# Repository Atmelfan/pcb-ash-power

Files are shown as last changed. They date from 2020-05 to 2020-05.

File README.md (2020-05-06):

# ASH Power distribution board

This board manages power control and distribution for my Octapod.

The power board has the following responsibilites:
* Regulate servo voltage from 2 or 3S Li-ion battery packs.
* Measure voltage and current to servos.
* Supply the main board with power (not regulated).
* Provide soft-start functionality for servos.
* Control power on/off to servos.
* Protect batteries with UVLO and OVLO.
~~* Integrated charger using external USB-C supply.~~
* Provide an interface for both main board MCU(I2C) and NVM(serial-SCPI).

[Schematic](https://github.com/Atmelfan/pcb-ash-power/raw/master/schematics.PDF)

[Assembly diagram](https://github.com/Atmelfan/pcb-ash-power/raw/master/assembly.PDF)

[Bill of material](https://htmlpreview.github.io/?https://github.com/Atmelfan/pcb-ash-power/blob/master/bom.html)

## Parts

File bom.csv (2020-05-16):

value | Line # | Name | Description | Designator | Quantity | Footprint | Manufacturer 1 | Manufacturer Part Number 1 | Manufacturer Lifecycle 1 | Supplier 1 | Supplier Part Number 1 | Supplier Unit Price 1 | Supplier Subtotal 1
 |  | INA3221 | Triple-Channel, High-Side Measurement. Shunt and Bus Voltage Monitor with I 2 C- and SMBUS-Compatible Interface | U1102, U1302, U1502, U1702, U2202, U2402, U2602, U2802 | 8 | QFN65P400X400X100_HS-17N_INA3221 | Texas Instruments | INA3221AIRGVR | Volume Production | Digi-Key | 296-INA3221AIRGVRDKR-ND | 39.18 | 313.42
 |  | ltc4421xuhe | High Power Prioritized PowerPath Controller | U3, U1004, U2004 | 3 | QFN50P500X600X80_HS-37N_LTC4421 | Analog Devices | LTC4421CUHE#PBF | Volume Production | Digi-Key | 161-LTC4421CUHE#PBF-ND | 96.86 | 290.59
 |  | EPC2030 | GaN Enhancement Mode Power Transistor | Q1006, Q1007, Q2006, Q2007 | 4 | epc2030_die | EPC | EPC2030ENGRT | Volume Production | Digi-Key | 917-EPC2030ENGRDKR-ND | 64.48 | 257.9
22u |  | cap | Capacitor | C1028-1031, C1037-1040, C2028-2031, C2037-2040 | 16 | CAPC3225X14N | Murata | GRM32ER71E226KE15L | Volume Production | Digi-Key | 490-5313-6-ND | 15.22 | 243.49
 |  | TPS1HB08A-Q1 | 40-V, 8-mO Single-Channel Smart High-Side Switch | U1100, U1300, U1500, U1700, U2200, U2400, U2600, U2800 | 8 | TSOP65P640X120_HS-17N_TPS1HB08 | Texas Instruments | TPS1HB08AQPWPRQ1 | Unknown | Digi-Key | 296-TPS1HB08AQPWPRQ1DKR-ND | 25.4 | 203.17
 |  | ltc7800 | Low IQ, 60V, High Frequency Synchronous Step-Down Controller | U1002, U2002 | 2 | QFN50P300X400X80_HS-21N_LTC7800 | Analog Devices / Linear Technology | LTC7800EUDC#PBF | Volume Production | Digi-Key | LTC7800EUDC#PBF-ND | 85.25 | 170.49
0R01 |  | res_4t | Resistor | R47, R1018, R1108, R1109, R1111, R1308, R1309, R1311, R1508, R1509, R1511, R1708, R1709, R1711, R2018, R2208, R2209, R2211, R2408, R2409, R2411, R2608, R2609, R2611, R2808, R2809, R2811 | 27 | 4T_RESC1632X05N | Cyntec | RL1632T4F-R010-FNH | Unknown | Digi-Key | 2037-RL1632T4F-R010-FNHDKR-ND | 6.03 | 162.76
 |  | SiR158DP | N-Channel 30 V (D-S) MOSFET | Q1008, Q1009, Q1011, Q1012, Q2008, Q2009, Q2011, Q2012 | 8 | SON127P620X112_HS-9N_POWERPAK_SO8 | Vishay Siliconix | SIR158DP-T1-GE3 | Volume Production | Digi-Key | SIR158DP-T1-GE3CT-ND | 17.72 | 141.75
 |  | LTC4370xMS | Two-Supply Diode-OR Current Balancing Controller | U4 | 1 | TSSOP50P510X110-16N_ltc4421 | Analog Devices / Linear Technology | LTC4370IMS#PBF | Volume Production | Digi-Key | LTC4370IMS#PBF-ND | 135.84 | 135.84
 |  | IRFH3702 | HEXFET Power MOSFET | Q9, Q10 | 2 | PQFN67P300X300X100-8N | International Rectifier | IRFH3702TRPBF | Volume Production | Digi-Key | IRFH3702TRPBFCT-ND | 55.23 | 110.46
 |  | pca9633dp2 | 4-bit Fm+ I2C-bus LED driver | U1101, U1301, U1501, U1701, U2201, U2401, U2601, U2801 | 8 | TSSOP50P490X110-10N_PCA9633DP2 | NXP Semiconductors | PCA9633DP2,118 | Volume Production | Digi-Key | 568-3237-6-ND | 13.09 | 104.74
 |  | 74LV4T125A | Quadruple Bus Buffer Gates With 3-State Outputs | U1103, U1303, U1503, U1703, U2203, U2403, U2603, U2803 | 8 | QFN50P350X350X100_HS-15N | Texas Instruments | SN74LV4T125RGYR | Volume Production | Digi-Key | 296-40546-1-ND | 9.45 | 75.6
 |  | ina219aidcnx | INA219 Zero-Drift, Bidirectional Current/Power Monitor With I2C Interface | U10, U1000, U2000 | 3 | TSOP65P280X145-8N | Texas Instruments | INA219AIDCNR | Volume Production | Digi-Key | 296-23770-1-ND | 23.23 | 69.69
1u |  | SER2009-102ML | Shielded Power Inductor | L1001, L2001 | 2 | SER20xx | Coilcraft | SER2009-102MLB | Volume Production | Mouser | 994-SER2009-102MLB | 25.1 | 50.2
 |  | STM32F103C8T6 | ARM Cortex-M3 32-bit MCU, 64 KB Flash, 20 KB Internal RAM, 37 I/Os, 48-pin LQFP, -40 to 85 degC, Tray | U2 | 1 | STM-LQFP48_N | STMicroelectronics | STM32F103C8T6 | Volume Production | Digi-Key | 497-6063-ND | 48.63 | 48.63
 |  | 430450617 | Micro-Fit 3.0 Vertical Header, 3.00mm Pitch, Dual Row, 6 Circuits, with PCB Press-fit Metal Retention Clip, Gold, Glow-Wire Capable, Black | J3 | 1 | 430450617 | Molex | 43045-0617 | Volume Production | Digi-Key | WM23255CT-ND | 39.08 | 39.08
 |  | DFLS2100 | 2.0A HIGH VOLTAGE SCHOTTKY BARRIER RECTIFIER | D11, D12, D17, D1000, D2000 | 5 | SODFL370X100-2N_DFLS2100 | Diodes Zetex | DFLS2100-7 | Volume Production | Digi-Key | DFLS2100-7DIDKR-ND | 5.61 | 28.05
 |  | 1054550101 | USB TYPE C REC MIDDLE MOUNT TYPE | J8 | 1 | 1054550101 | Molex | 105455-0101 | Unknown | Digi-Key | WM17904DKR-ND | 23.72 | 23.72
 |  | pca9685bs | 16-channel, 12-bit PWM Fm+ I2C-bus LED controller | U8 | 1 | QFN65P600X600X100_HS-29N_PCA9685BS | NXP USA | PCA9685BS,118 | Unknown | Digi-Key | 568-5305-6-ND | 23.43 | 23.43
 |  | IRFH3702 | HEXFET Power MOSFET | Q5-8 | 4 | PQFN67P300X300X100-8N | International Rectifier | IRFH3702TRPBF | Volume Production | Digi-Key | IRFH3702TRPBFCT-ND | 5.61 | 22.44
 |  | bq2961xx | BQ296xxx Overvoltage Protection for 2-Series, 3-Series, and 4-Series Cell Li-Ion Batteries with Regulated Output Supply | U1003, U2003 | 2 | SON50P200X80_HS-9N-BQ2960XX | Texas Instruments | BQ296106DSGT | Volume Production | Digi-Key | 296-BQ296106DSGTDKR-ND | 9.84 | 19.69
22u |  | cap | Capacitor | C2, C3, C34, C35 | 4 | CAPC3216X14N | Samsung | CL31A226KAHNNNE | Volume Production | Digi-Key | 1276-3047-6-ND | 4.82 | 19.29
1m5 |  | res_4t | Resistor | R16, R1028, R2028 | 3 | 4T_RESC1632X05N | Cyntec | RL1632T4F-R001-FNH | Unknown | Digi-Key | 2037-RL1632T4F-R001-FNHDKR-ND | 5.91 | 17.72
3m3 |  | SRR4028 |  | L1, L2 | 2 | SRR4028 | Bourns | SRR4028-3R3Y | Volume Production | Digi-Key | SRR4028-3R3YCT-ND | 8.56 | 17.13
 |  | BAS40-5 | Diode Common Cathode | D2, D3, D7, D8, D13, D1003, D2003 | 7 | SOT23_CC | Diodes | BAS40-05-7-F | Volume Production | Digi-Key | BAS40-05FDIDKR-ND | 2.36 | 16.54
 |  | RU1J002YN | N-channel 50V 200mA Small signal MOSFET | Q2-4, Q12-16, Q1010, Q2010 | 10 | SOTFL65P210X105-3N | Rohm | RU1J002YNTCL | Volume Production | Digi-Key | RU1J002YNTCLCT-ND | 1.6 | 16.05
 |  | ESDA25W | TRANSIL array for data protection | D9, D14-16 | 4 | SOT65P210X110-3N_SOT323-3L | STMicroelectronics | ESDA25W | Volume Production | Digi-Key | 497-6689-6-ND | 3.94 | 15.75
 |  | S4B-XH-SM4-TB | 2.5mm pitch/Disconnectable Crimp style connectors | J1000, J2000 | 2 | S4B-XH-SM4-TB | JST | S4B-XH-SM4-TB-(LF)(SN) | Volume Production | Digi-Key | 455-2262-6-ND | 7.68 | 15.36
100n |  | cap | Capacitor | C1, C4, C11-16, C23-25, C28, C30-33, C36, C40, C41, C46-48, C1026, C1036, C1041-1043, C1047, C1048, C1050, C1057, C1100-1102, C1300-1302, C1500-1502, C1700-1702, C2026, C2036, C2041-2043, C2047, C2048, C2050, C2057, C2200-2202, C2400-2402, C2600-2602, C2800-2802 | 64 | CAPC1005X06N | Yageo | CC0402KRX7R7BB104 | Volume Production | Digi-Key | 311-1338-1-ND | 0.14766 | 14.77
 |  | IRFHM9331 | HEXFET Power MOSFET | Q17, Q18 | 2 | PQFN67P300X300X100-8N | International Rectifier | IRFHM9331TRPBF | Volume Production | Digi-Key | IRFHM9331TRPBFCT-ND | 7.09 | 14.17
2m |  | res | Resistor | R30, R36 | 2 | RESC3216X07N | Rohm | PMR18EZPJV2L0 | Volume Production | Digi-Key | RHM.002AMDKR-ND | 6 | 12.01
10u |  | cap | Capacitor | C5, C6, C9, C37, C38 | 5 | CAPC3216X14N | Samsung | CL31A106KAHNNNE | Volume Production | Digi-Key | 1276-1075-6-ND | 2.36 | 11.81
 |  | tps56120x | 4.5-V to 17-V Input, 1-A Synchronous Step-Down Voltage Regulator in 6-Pin SOT-23 | U1, U7 | 2 | SOT95P280X110-6N | Texas Instruments | TPS561201DDCR | Unknown | Digi-Key | 296-47885-6-ND | 5.81 | 11.62
 |  | tca9543a | Low Voltage 2-Channel I2C Bus Switch With Interrupt Logic And Reset | U5 | 1 | TSOP65P640X120-14N_PCA9543A | Texas Instruments | TCA9543APWR | Volume Production | Digi-Key | 296-42157-6-ND | 11.42 | 11.42
470n |  | cap | Capacitor | C1046, C2046 | 2 | CAPC2012X11N | Kyocera AVX | 08053D474KAT2A | Volume Production | Digi-Key | 478-1407-6-ND | 5.71 | 11.42
47n |  | cap | Capacitor | C18, C22, C26, C29, C1044, C1049, C1052, C1056, C2044, C2049, C2052, C2056 | 12 | CAPC1005X06N | Yageo | AC0402KRX7R8BB473 | Unknown | Digi-Key | 311-3071-6-ND | 0.77765 | 9.33
 |  | NTS12100EMFS | Very Low LeakageTrench-based SchottkyRectifier | D1002, D2002 | 2 | SON127P620X110_HS-9N_NTS12100 | ON Semiconductor | NTS12100EMFST1G | Not Recommended for New Design | Mouser | 863-NTS12100EMFST1G | 4.33 | 8.66
 |  | diode | Diode | D1001, D2001 | 2 | CAPCP1005X06N | Diodes | BZT52C5V1LP-7 | Volume Production | Digi-Key | BZT52C5V1LP-7DIDKR-ND | 4.23 | 8.47
2u2 |  | cap | Capacitor | C1027, C2027 | 2 | CAPC2012X11N | Kyocera AVX | 08053C225KAT2A | Volume Production | Digi-Key | 478-5719-6-ND | 3.74 | 7.48
 |  | Si3493DDV | P-Channel 20 V (D-S) MOSFET | Q1, Q11 | 2 | SOT95P284X110-6N_TSOP6 | Vishay | SI3493DDV-T1-GE3 | Unknown | Digi-Key | SI3493DDV-T1-GE3DKR-ND | 3.64 | 7.28
0R1 |  | res_4t | Resistor | R70 | 1 | RESC2012X06N_4T | Panasonic | ERJ-6BWFR010V | Volume Production | Digi-Key | P.01AQCT-ND | 6.4 | 6.4
 |  | INA180A1 | Low- and High-Side Voltage Output, Current-Sense Amplifiers | U6 | 1 | SOT95P280X145-5N | Texas Instruments | INA180A1IDBVR | Unknown | Digi-Key | 296-47652-1-ND | 6.3 | 6.3
1n |  | cap | Capacitor | C10, C21, C1055, C2055 | 4 | CAPC1005X06N | Murata | GRM1555C1H102JA01D | Volume Production | Digi-Key | 490-3244-6-ND | 1.18 | 4.72
0R |  | res | Resistor | ID1100-1104, ID1300-1304, ID1500-1504, ID1700-1704, ID2200-2204, ID2400-2404, ID2600-2604, ID2800-2804, R65, R67, R68, R1000, R1020, R1026, R1036, R2000, R2020, R2026, R2036 | 51 | RESC1005X04N | Yageo | RC0402JR-070RL | Volume Production | Digi-Key | 311-0.0JRDKR-ND | 0.07087 | 3.61
 |  | FA-238 | Crystal With Shield | X1 | 1 | DFN220P320X70-4N | Epson | FA-23824.0000MB-C3 | Volume Production | Digi-Key | SER3689CT-ND | 3.54 | 3.54
1R21 |  | res | Resistor | R23, R32 | 2 | RESC2012X06N | Yageo | RC0805FR-071R21L | Volume Production | Digi-Key | 311-1.21CRDKR-ND | 0.98437 | 1.97
10R |  | res | Resistor | R1019, R2019 | 2 | RESC2012X06N | Yageo | RC0805FR-0710RL | Volume Production | Digi-Key | 311-10.0CRDKR-ND | 0.98437 | 1.97
82p |  | cap | Capacitor | C1035, C2035 | 2 | CAPC1005X06N | Murata | GRM1555C1H820JA01D | Volume Production | Digi-Key | 490-5879-6-ND | 0.98437 | 1.97
100n |  | cap | Capacitor | C1033, C2033 | 2 | CAPC1608X08N | Yageo | CC0603KRX7R9BB104 | Volume Production | Digi-Key | 311-1344-6-ND | 0.98437 | 1.97
820p |  | cap | Capacitor | C1034, C2034 | 2 | CAPC1005X06N | Murata | GRM155R71H821KA01D | Volume Production | Digi-Key | 490-3250-6-ND | 0.98437 | 1.97
 |  | 2x5 | 2x5 Header | J1, JG1000, JG1001, JG2000, JG2001 | 5 | hdr_2x5_50mil
 |  | Header 1x3 | 2.54mm pitch single row header | J4-7, JS1100-1102, JS1300-1302, JS1500-1502, JS1700-1702, JS2200-2202, JS2400-2402, JS2600-2602, JS2800-2802 | 28 | HEADER_1x3_100MIL
 |  | M3 | Mounting hole | MH1-6 | 6 | mount_m3_normal
 |  | STUSB4500 | Standalone USB PD sink controller with short-to-VBUS protections | U9 | 1 | QFN50P400X400X100_HS-25N-STUSB4500 | STMicroelectronics | STUSB4500QTR | Unknown
 |  | SWD | SWD Header | J2 | 1 | hdr_2x5_50mil
 |  | XT60PT-M |  | P1, P2 | 2 | XT60PT-M
1K |  | res | Resistor | R60 | 1 | RESC2012X06N
1K |  | res | Resistor | R62, R1033, R1035, R1038, R2033, R2035, R2038 | 7 | RESC1005X04N
1K2 |  | res | Resistor | R1024, R2024 | 2 | RESC1005X04N
1M |  | res | Resistor | R6, R7, R18, R22, R26, R31, R38, R69, R1040, R1041, R2040, R2041 | 12 | RESC1005X04N
1R21 |  | res | Resistor | R1030, R2030 | 2 | RESC1005X04N
1u |  | cap | Capacitor | C17, C19, C20, C27, C42-45, C1045, C1051, C1054, C2045, C2051, C2054 | 14 | CAPC2012X11N | Murata | GRM216R61E105KA12D | Volume Production
4K99 |  | res | Resistor | R1021, R2021 | 2 | RESC1005X04N
5K49 |  | res | Resistor | R25, R34, R1032, R1046, R2032, R2046 | 6 | RESC1005X04N
10K |  | res | Resistor | R2, R5, R8-15, R17, R19-21, R29, R41-45, R48, R50, R52, R54, R72, R74, R1027, R1047, R1100-1105, R1300-1305, R1500-1505, R1700-1705, R2027, R2047, R2200-2205, R2400-2405, R2600-2605, R2800-2805 | 78 | RESC1005X04N
10R |  | res | Resistor | R1042, R2042 | 2 | RESC1005X04N
12K |  | res | Resistor | R1025, R2025 | 2 | RESC1005X04N
22K |  | res | Resistor | R61 | 1 | RESC1005X04N
31K6 |  | res | Resistor | R27, R35, R1034, R1048, R2034, R2048 | 6 | RESC1005X04N
33K |  | res | Resistor | R3, R49 | 2 | RESC1005X04N
39K7 |  | res | Resistor | R28, R37, R1037, R1050, R2037, R2050 | 6 | RESC1005X04N
65K |  | res | Resistor | R1023, R2023 | 2 | RESC1005X04N
100K |  | res | Resistor | R4, R57, R63, R64, R66, R1001, R1022, R1039, R1106, R1107, R1110, R1306, R1307, R1310, R1506, R1507, R1510, R1706, R1707, R1710, R2001, R2022, R2039, R2206, R2207, R2210, R2406, R2407, R2410, R2606, R2607, R2610, R2806, R2807, R2810 | 35 | RESC1005X04N
100R |  | ferrite | Inductor | FB1, FB1000, FB1001, FB2000, FB2001 | 5 | INDC1005X06N
100R |  | res | Resistor | R51, R53, R55, R56, R59, R1029, R2029 | 7 | RESC1005X04N
190K |  | res | Resistor | R71, R73 | 2 | RESC1005X04N
220R |  | res | Resistor | R39, R40 | 2 | RESC1005X04N
470K |  | res | Resistor | R1, R46 | 2 | RESC1005X04N
470R |  | res | Resistor | R58 | 1 | RESC2012X06N
920K |  | res | Resistor | R24, R33, R1031, R1045, R2031, R2045 | 6 | RESC1005X04N
DNP |  | cap | Capacitor | C7, C8, C39 | 3 | CAPC1005X06N
GREEN |  | led | LED | D6, D1100, D1300, D1500, D1700, D2200, D2400, D2600, D2800 | 9 | CAPCP1005X06N
RED |  | led | LED | D1102, D1302, D1502, D1702, D2202, D2402, D2602, D2802 | 8 | CAPCP1005X06N
YELLOW |  | led | LED | D1101, D1301, D1501, D1701, D2201, D2401, D2601, D2801 | 8 | CAPCP1005X06N

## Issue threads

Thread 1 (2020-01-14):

Revision 1

Atmelfan, 2020-01-14:
Must have:
- Servo supplies
- Battery connections
- Battery UVLO protection
- Current & voltage measurement
- Local controller

Nice to have:
- Battery chargers
- RS485 smart-servo support

Atmelfan, 2020-01-15:
Must have two battery connections with hotswap (replacing one battery while system continius uninterrupted).

Atmelfan, 2020-01-28:
Redundant

Closed 2020-01-28.

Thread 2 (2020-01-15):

Power priority

Atmelfan, 2020-01-15:
# Servo supply
The left and right servo main switch should choose power source based on priority below:
1. Same side pack if valid
2. Other side pack if valid
3. Both invalid, turn off.

Where valid means pack voltage within UVL, OVL and cells balanced (V_cell\<highest> - V_cell\<lowest> < V_delta).

# Auxilliary supply
Auxilliary switch should choose according to below:
1. VBUS if valid
2. Left/right (diode-OR) pack if valid
3. No valid, turn off.

Valid might be more lenient than with servo supply to ensure servos shut off first.

# External supply
External switch should follow Auxilliary priority but disabled if servo supplies are turned off.

Atmelfan, 2020-01-15:
Servo supplies might use LTC4421 controller.

Atmelfan, 2020-01-17:
External power can use LTC4370 to share load between left and right packs. Sharing must be disabled when any one off the packs becomes unbalanced or UVLO.

Atmelfan, 2020-01-19:
Done

Closed 2020-01-19.

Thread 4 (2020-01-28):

Servo supplies

Atmelfan, 2020-01-28:
Servo supplies must be regulated down from 7.4 - 11.2 V battery voltage to 6 V maximum rated servo voltage.

Closed 2020-01-28.

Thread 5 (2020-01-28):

Battery connections

Atmelfan, 2020-01-28:
Batteries must have AMASS XT60 power and JST-XH balance lead connectors.

Atmelfan, 2020-01-28:
Batteries must be at least 2S and support for 3S would be nice.

Closed 2020-01-28.

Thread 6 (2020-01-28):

Current & voltage measurement

Atmelfan, 2020-01-28:
Servos must have individual current measurement (for torque estimation) and voltage monitoring.

Closed 2020-04-07.

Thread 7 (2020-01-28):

Local controller

Atmelfan, 2020-01-28:
Must have a local controller which can communicate with main CPU the following:
* Battery voltage & status
* Servo current
* Servo switches
Additionally a SCPI interface must be exposed to the NVM through a serial link.

Closed 2020-01-28.

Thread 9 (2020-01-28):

RS485 smart-servo support

Atmelfan, 2020-01-28:
Support for RS485 smart servos would be nice. These would not require current monitoring and optional voltage regulation.

Closed 2020-04-07.

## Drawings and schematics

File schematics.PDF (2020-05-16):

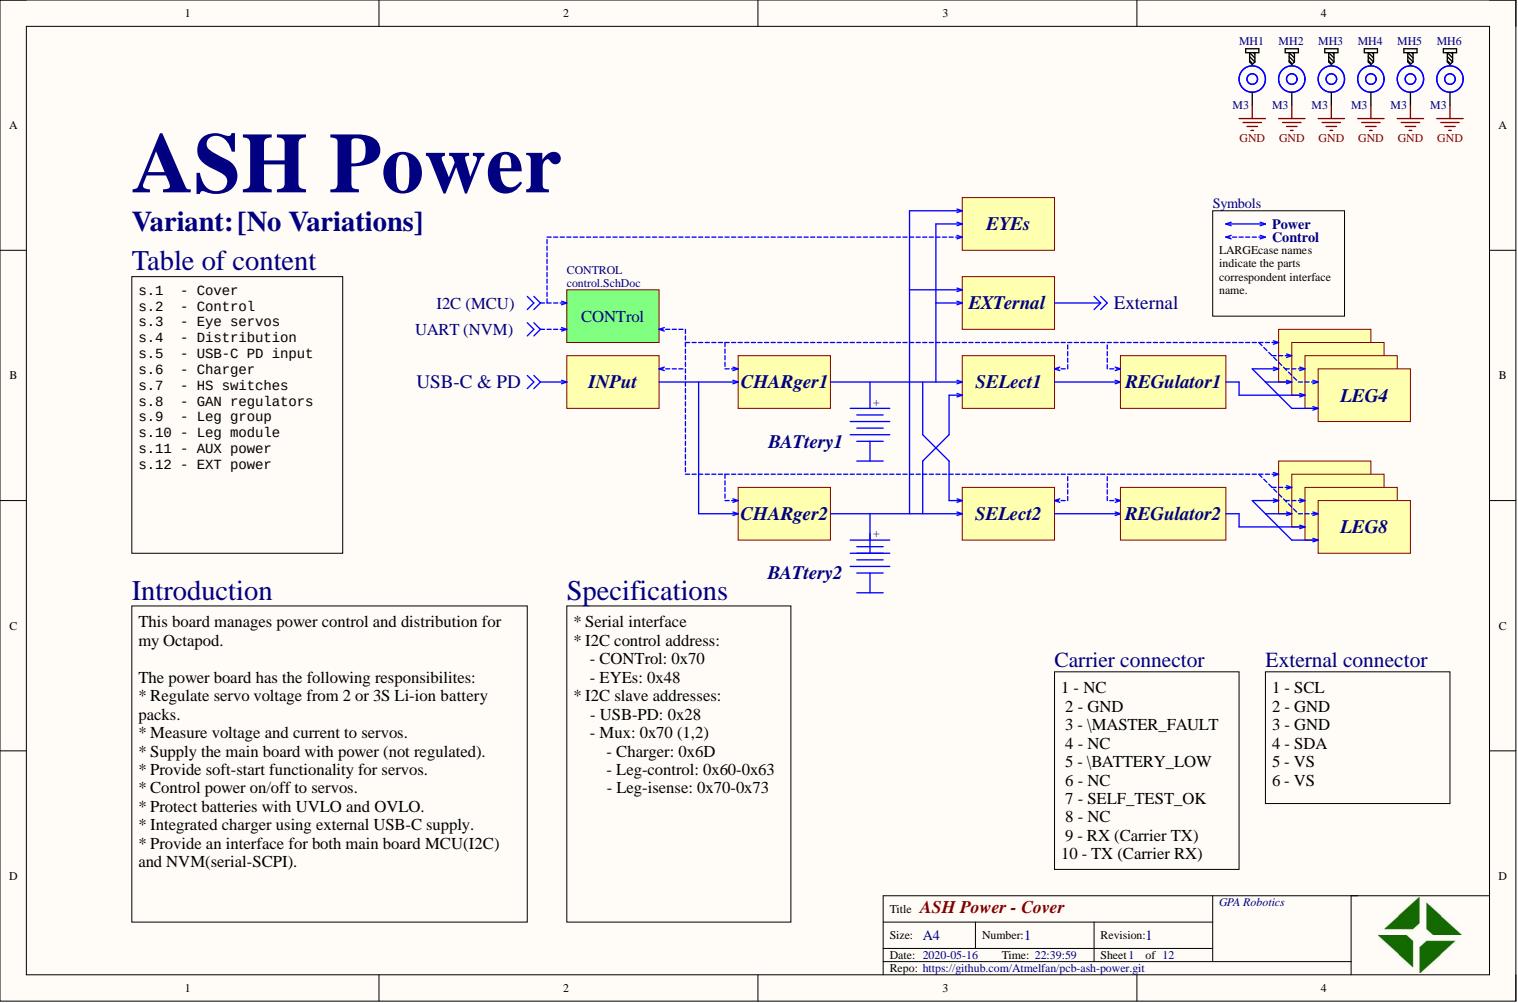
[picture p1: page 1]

This board manages power control and distribution for
my Octapod.

The power board has the following responsibilites:
* Regulate servo voltage from 2 or 3S Li-ion battery
packs.
* Measure voltage and current to servos.
* Supply the main board with power (not regulated).
* Provide soft-start functionality for servos.
* Control power on/off to servos.
* Protect batteries with UVLO and OVLO.
* Integrated charger using external USB-C supply.
* Provide an interface for both main board MCU(I2C)
and NVM(serial-SCPI).

Size: A4 | Number: | Revision:
Date: 2020-05-16 Time: 22:39:59 | | Sheet of

https://github.com/Atmelfan/pcb-ash-power.git

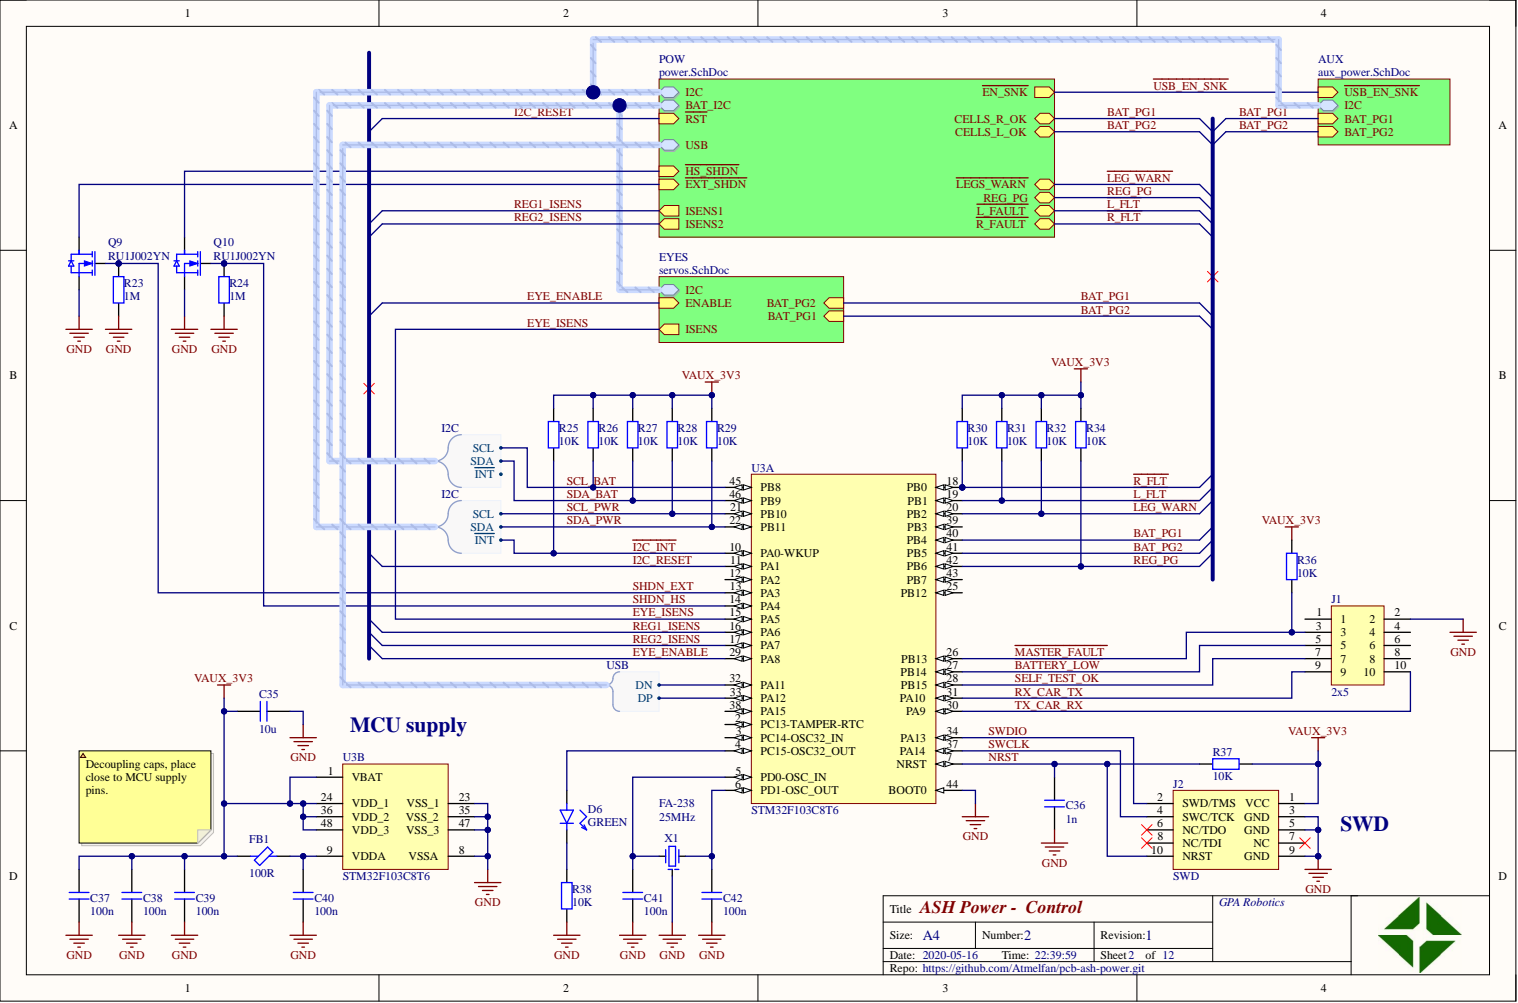
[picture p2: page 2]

EYES
servos.SchDoc
I2C ENABLE ISENS | BAT_PG2 BAT_PG1

SCL_BAT
SDA_BAT | | | | PB9 46
SCL_PWR | | | | PB10 21
SDA_PWR | | | | PB11 22

PA0-WKUP 10

SHDN_EXT | | PA2 12

SHDN_HS | PA4 14
EYE_ISENS | PA5 15

BATTERY_LOW
SELF_TEST_OK

PA12 33 | | RX_CAR_TX
PA15 38 | | TX_CAR_RX

PC15-OSC32_OUT 4 | SWCLK
PD0-OSC_IN 5 | NRST

Decoupling caps, place
close to MCU supply
pins.

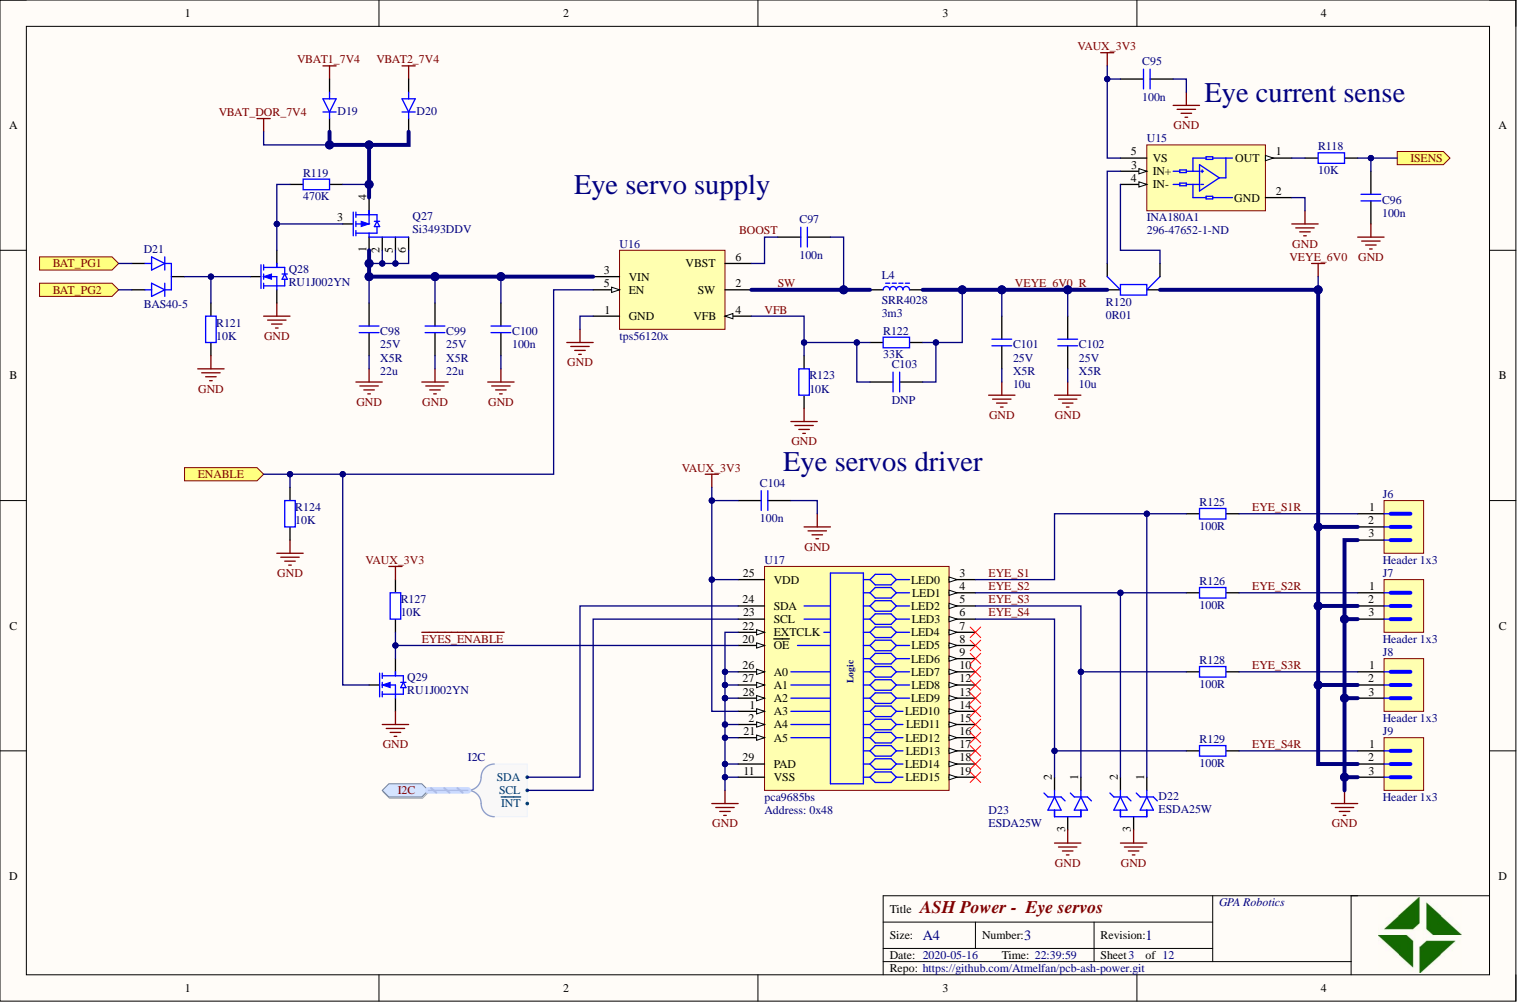
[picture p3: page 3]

IN+ 3
IN- 4

GND 1 | VFB

VAUX_3V3

VDD 25

EYE_S3 | 2

A0 26
A1 27 | 2

A3 1
A4 2
A5 21

PAD 29

ASH Power - Eye servos
Title

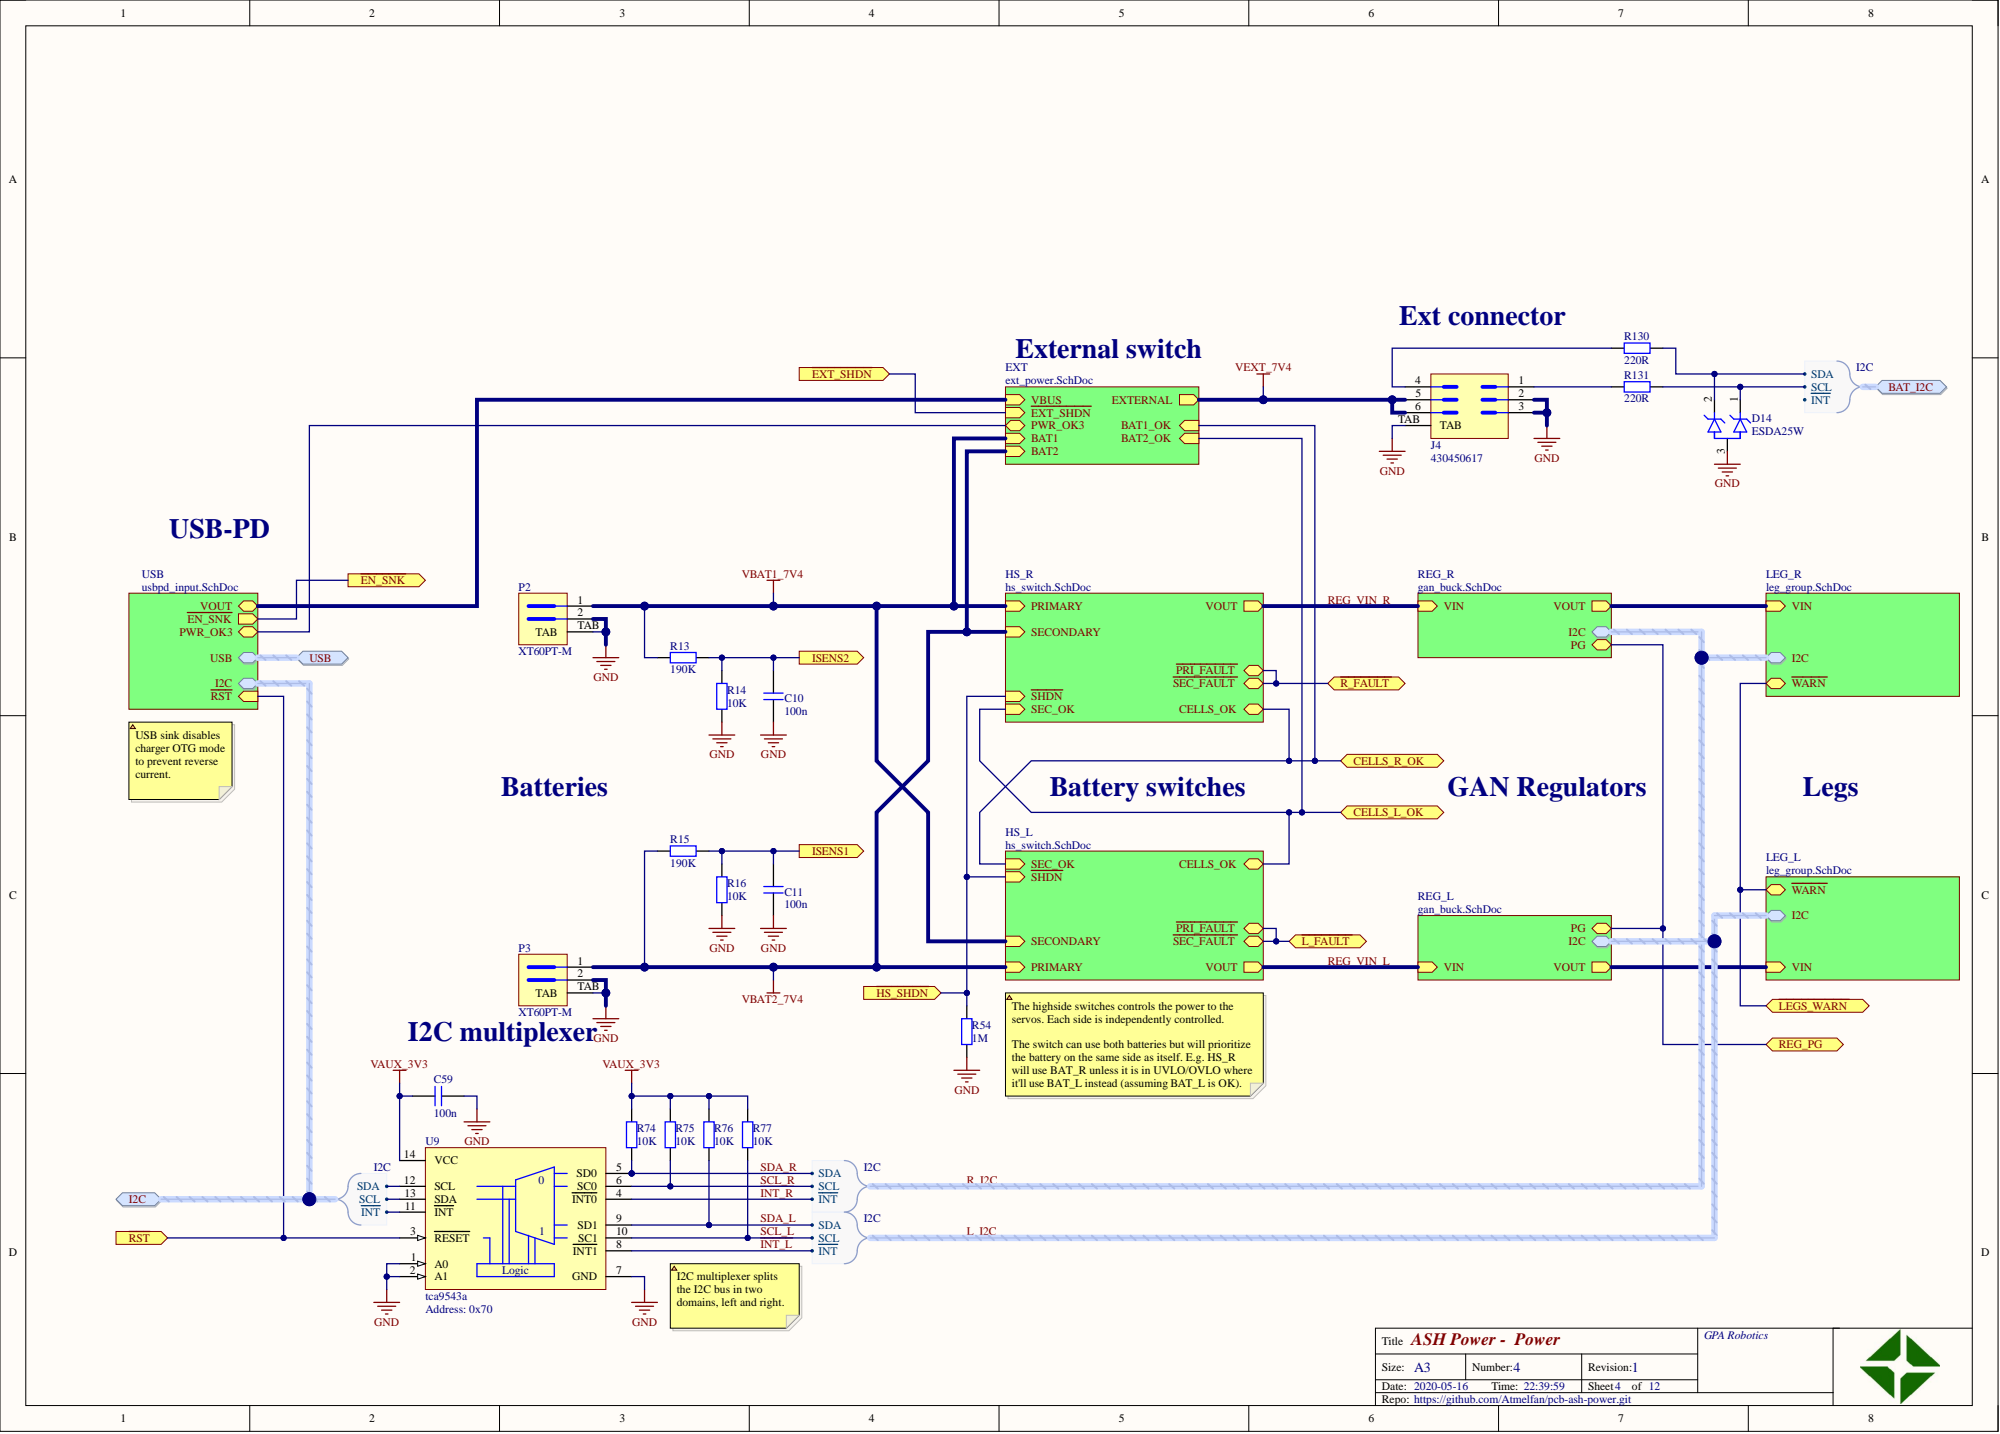
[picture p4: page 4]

The highside switches controls the power to the
servos. Each side is independently controlled.

The switch can use both batteries but will prioritize
the battery on the same side as itself. E.g. HS_R
will use BAT_R unless it is in UVLO/OVLO where
it'll use BAT_L instead (assuming BAT_L is OK).

I2C multiplexer splits
the I2C bus in two
domains, left and right.

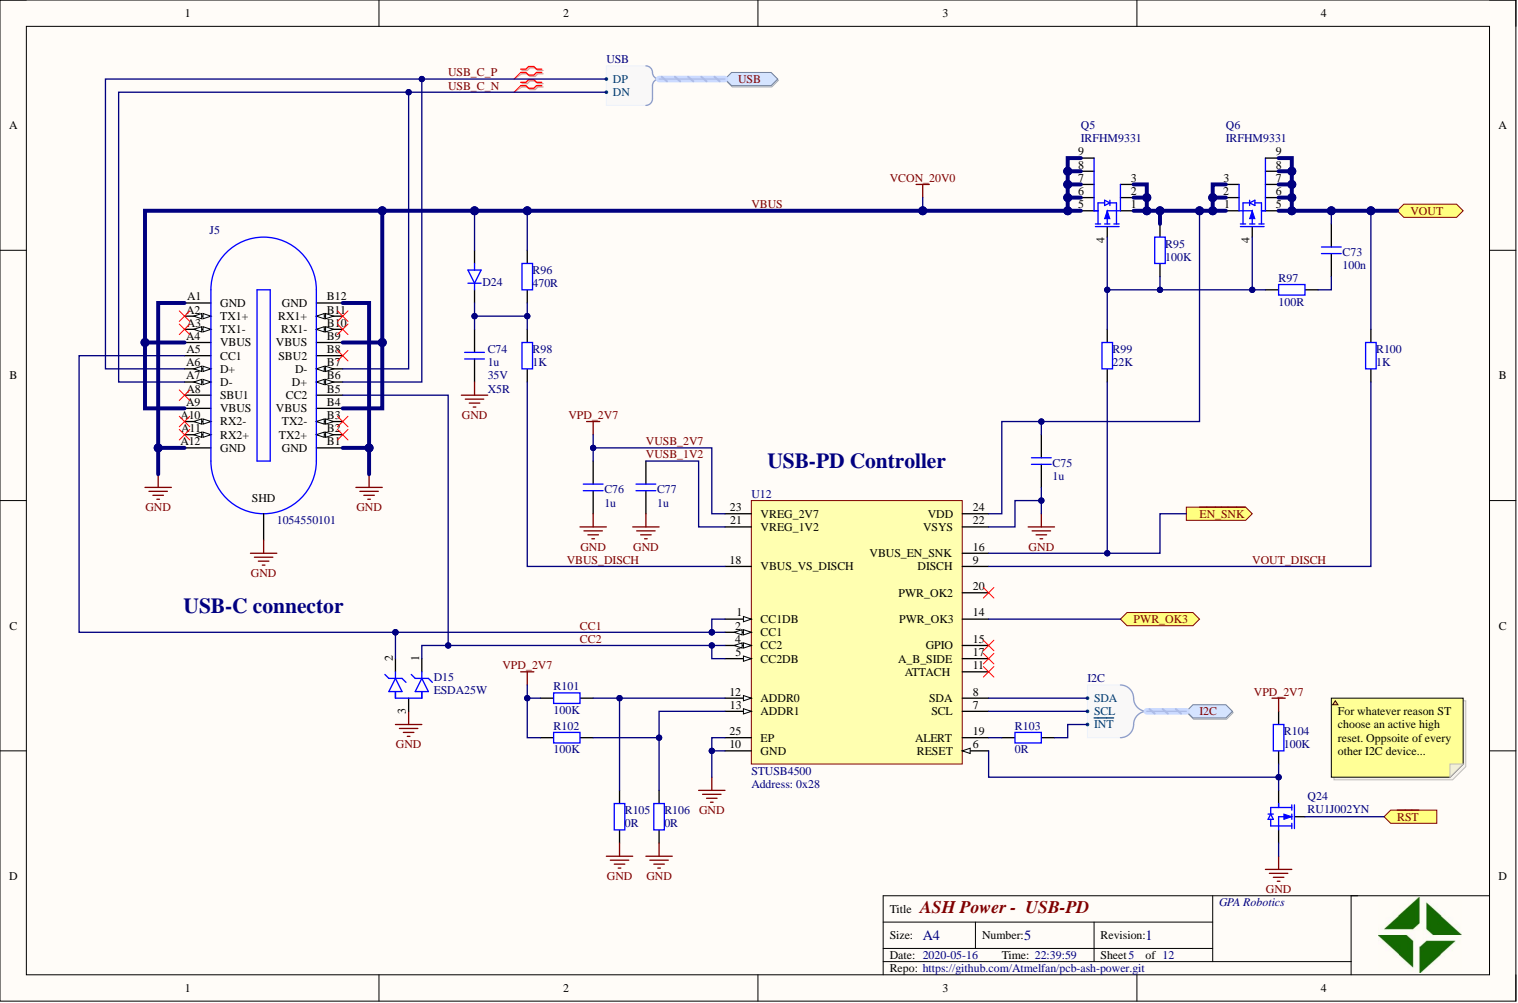
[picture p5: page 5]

CC1 A5
D+ A6
D- A7

ADDR1 13

For whatever reason ST
choose an active high
reset. Oppsoite of every
other I2C device...

GND 10

ASH Power - USB-PD
Title

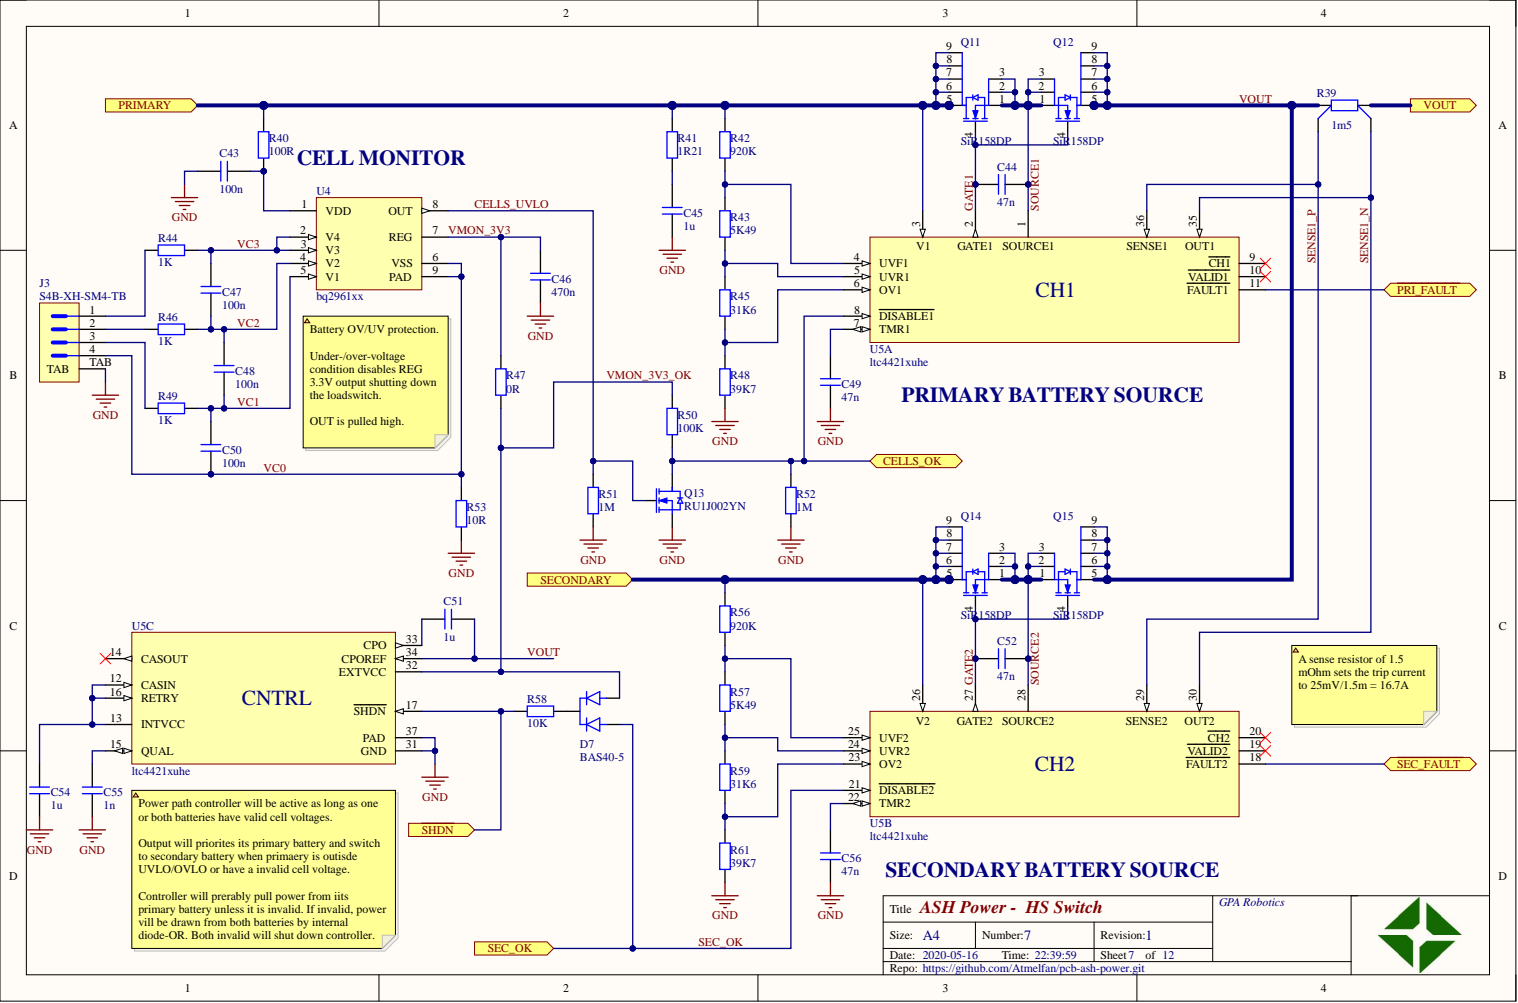
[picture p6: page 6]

Battery OV/UV protection.

OUT is pulled high.

A sense resistor of 1.5 mOhm sets the trip current

Power path controller will be active as long as one
or both batteries have valid cell voltages.

TMR2 22

Output will priorites its primary battery and switch
to secondary battery when primaery is outisde
UVLO/OVLO or have a invalid cell voltage.

Controller will prerably pull power from iits
primary battery unless it is invalid. If invalid, power vill be drawn from both batteries by internal

ASH Power - HS Switch 7

diode-OR. Both invalid will shut down controller

Time: | Sheet of

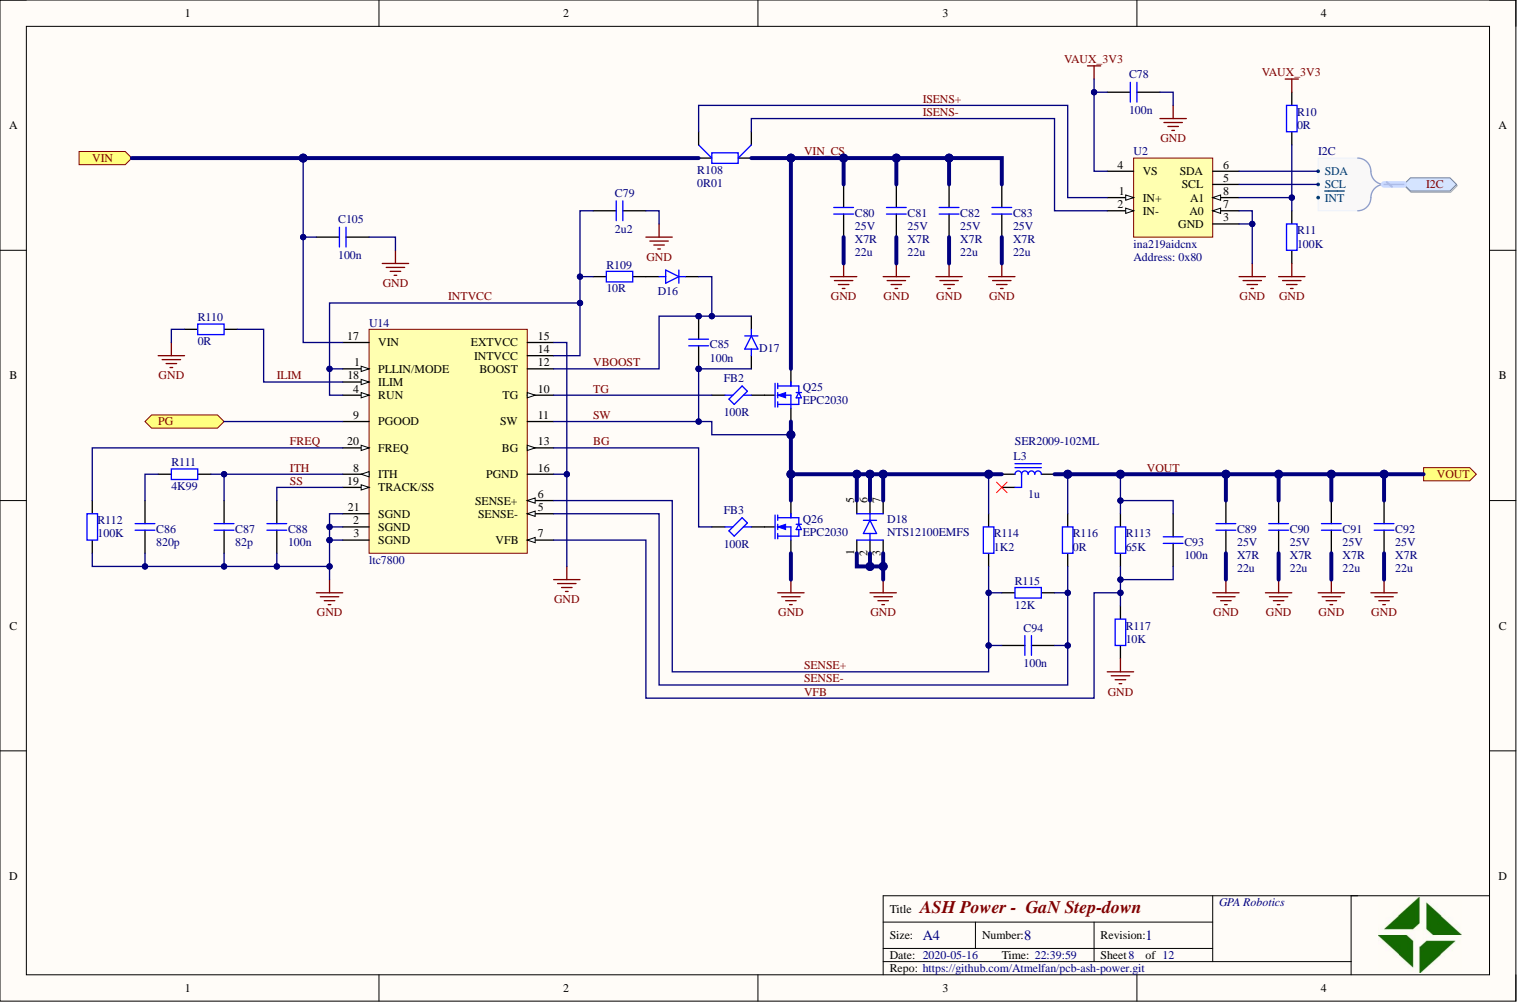
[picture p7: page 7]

ISENS-

VIN_CS

PLLIN/MODE 1

RUN 4

ASH Power - GaN Step-down
Title

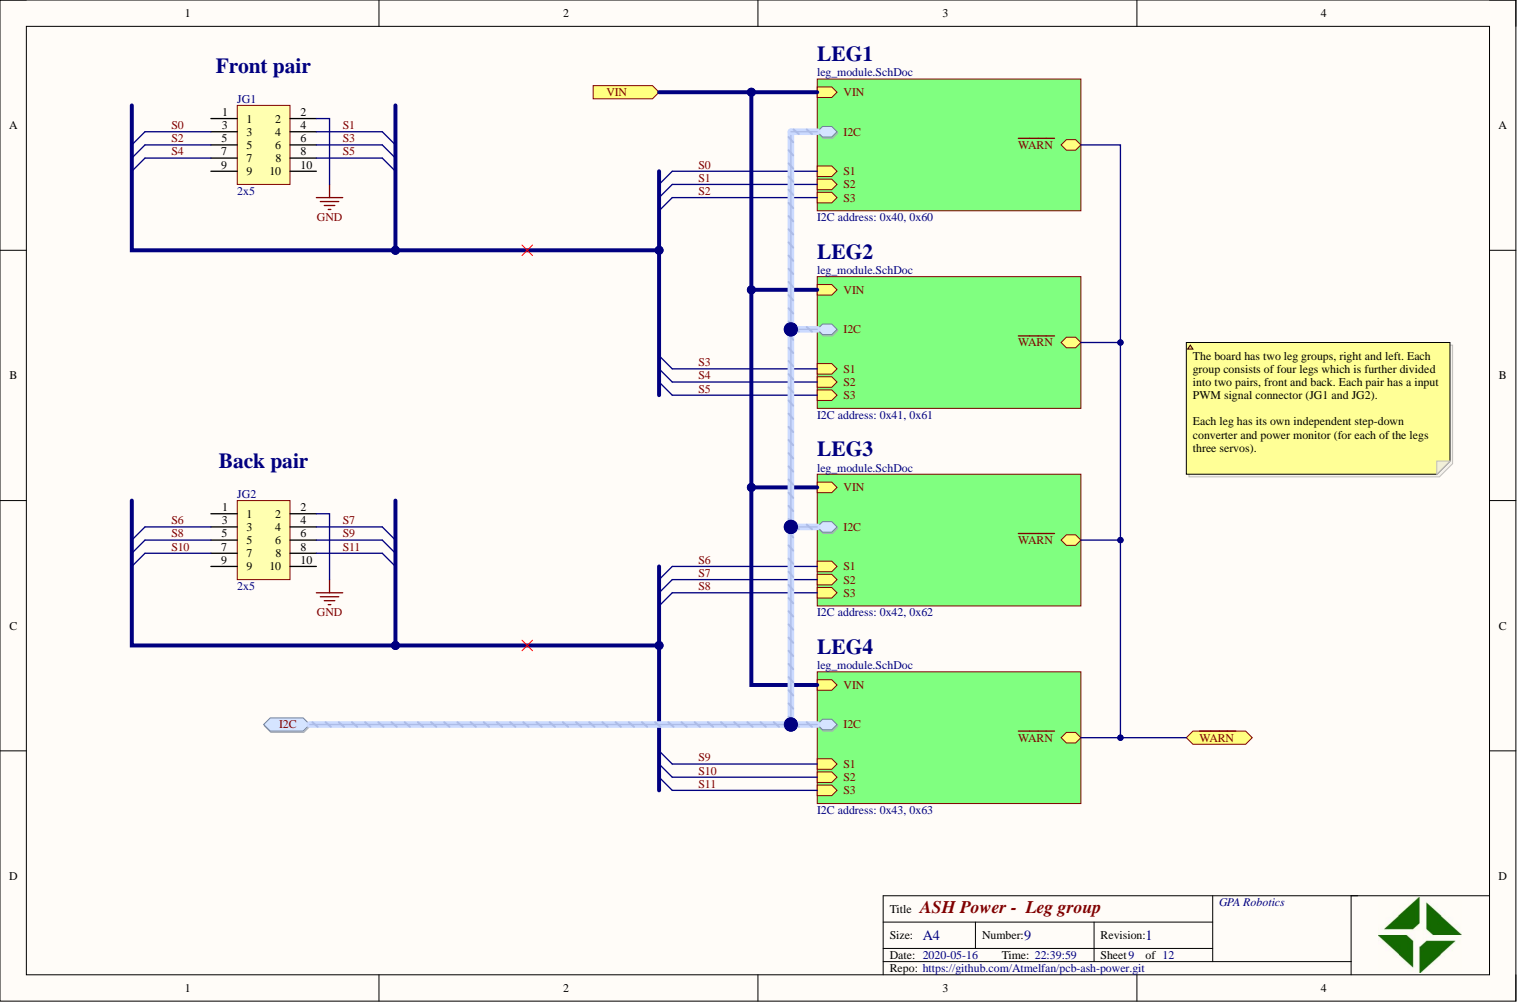
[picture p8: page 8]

1 1 2 3 3 4 5 5 6 7 7 8 | 2

The board has two leg groups, right and left. Each
group consists of four legs which is further divided
into two pairs, front and back. Each pair has a input
PWM signal connector (JG1 and JG2).

Each leg has its own independent step-down
converter and power monitor (for each of the legs
three servos).

ASH Power - Leg group
Title

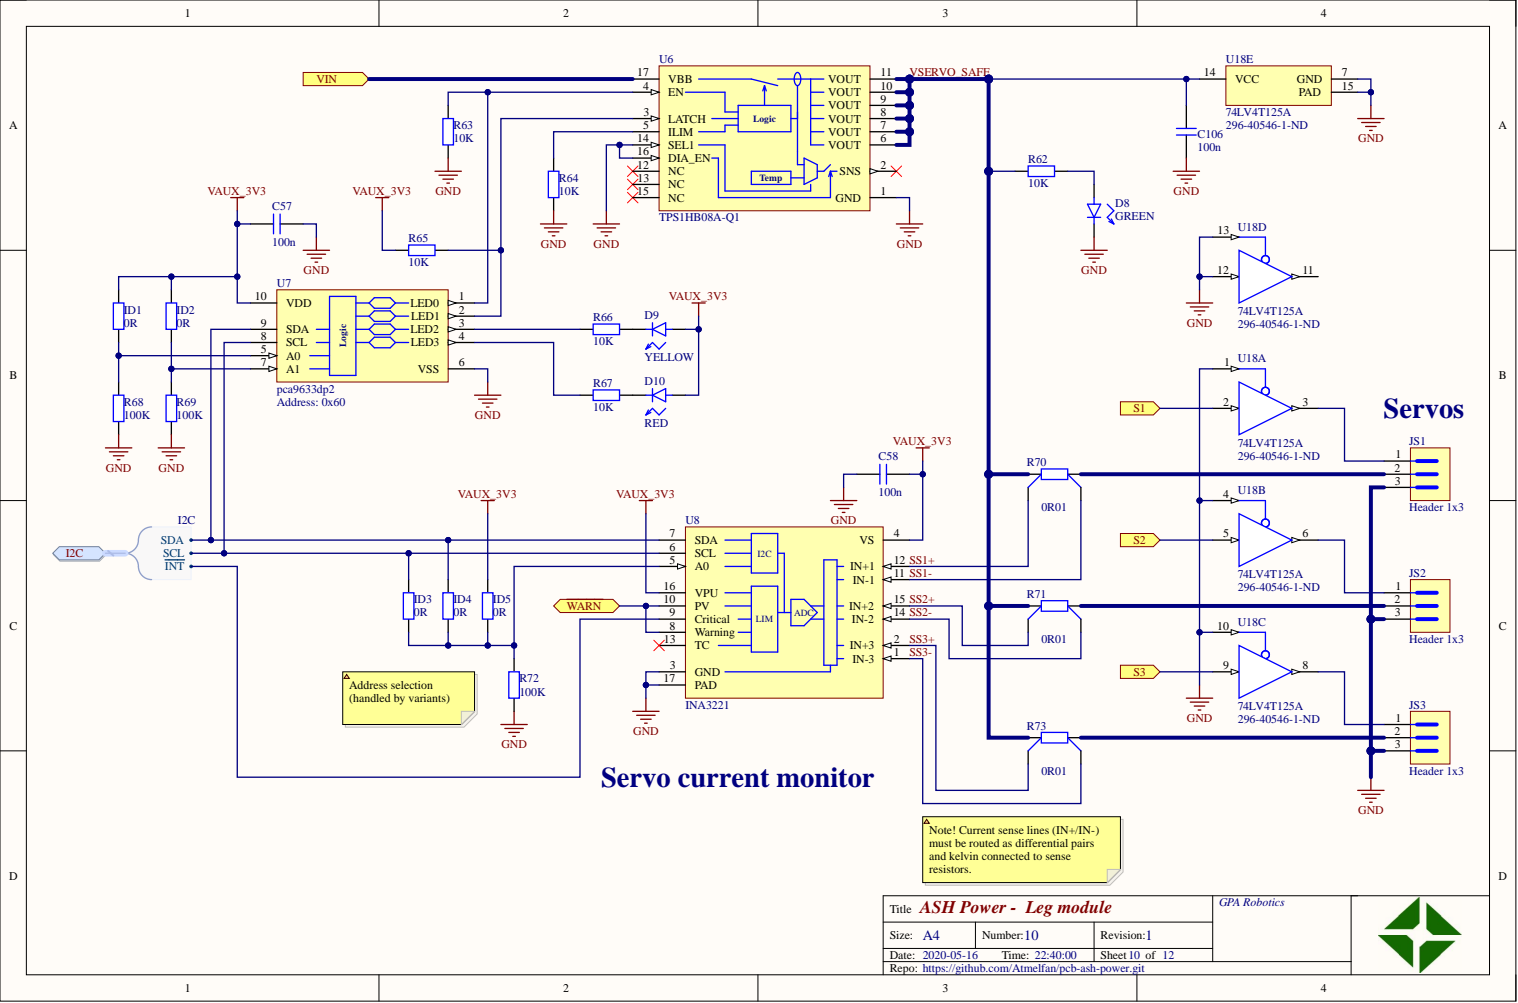
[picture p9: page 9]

VDD 10

Note! Current sense lines (IN+/IN-) must be routed as differential pairs

and kelvin connected to sense
resistors.

ASH Power - Leg module

2020-05-16 Time: 22:40:00 | Sheet of

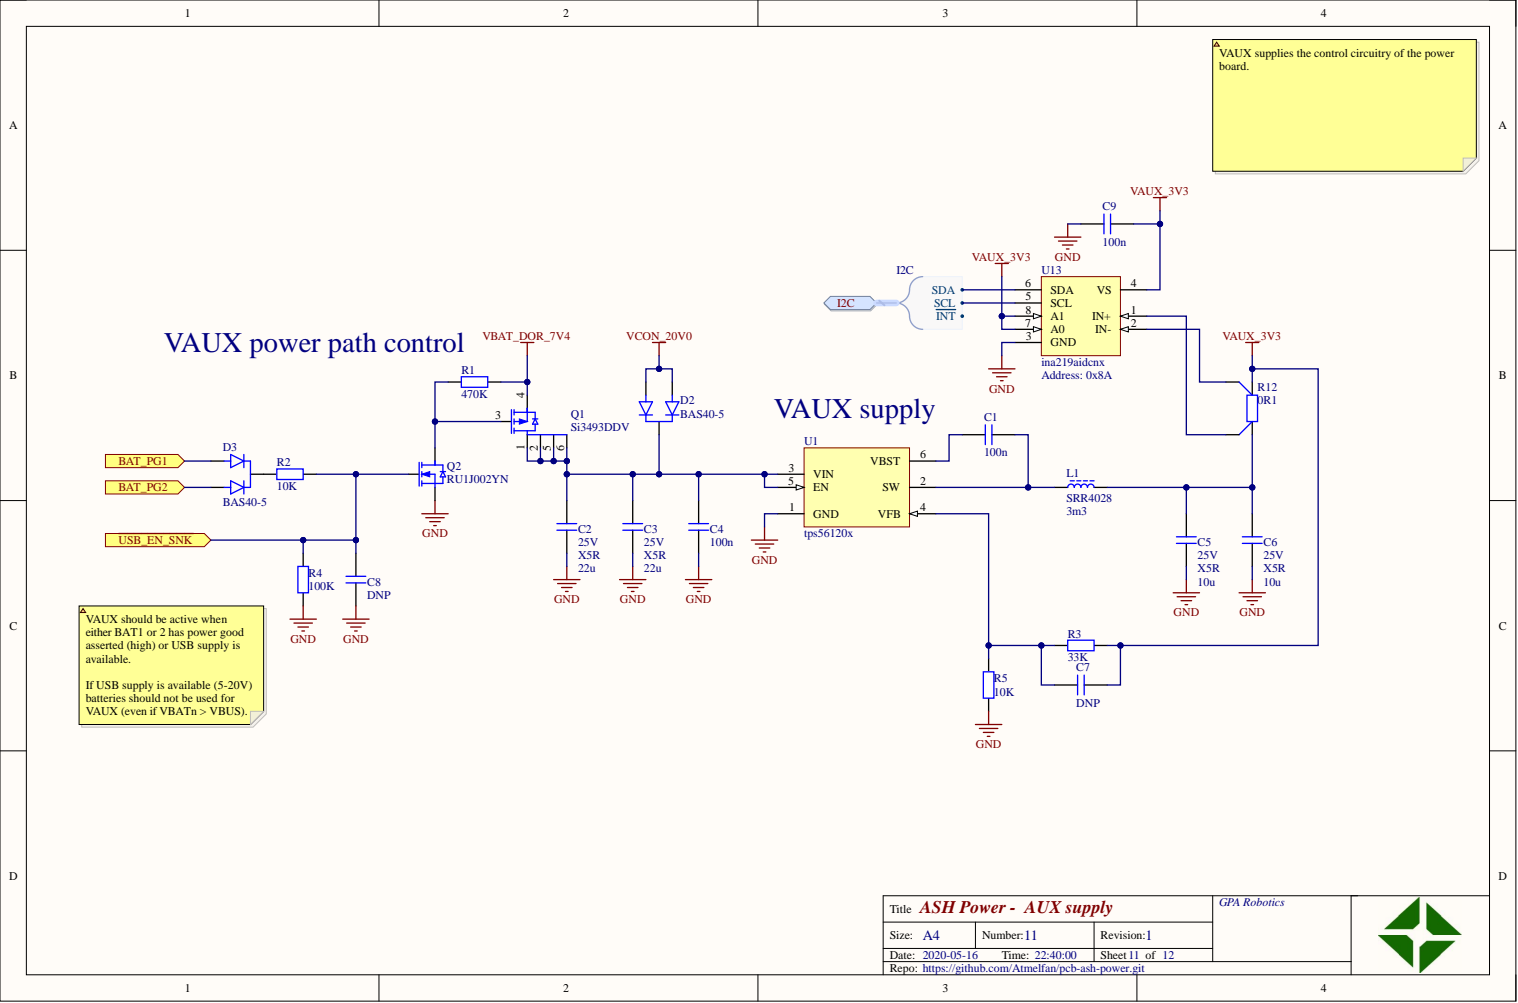
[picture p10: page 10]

VAUX supplies the control circuitry of the power
board.

VAUX power path control

GND 3

VAUX should be active when
either BAT1 or 2 has power good
asserted (high) or USB supply is
available.

If USB supply is available (5-20V)
batteries should not be used for
VAUX (even if VBATn > VBUS).

ASH Power - AUX supply
Title

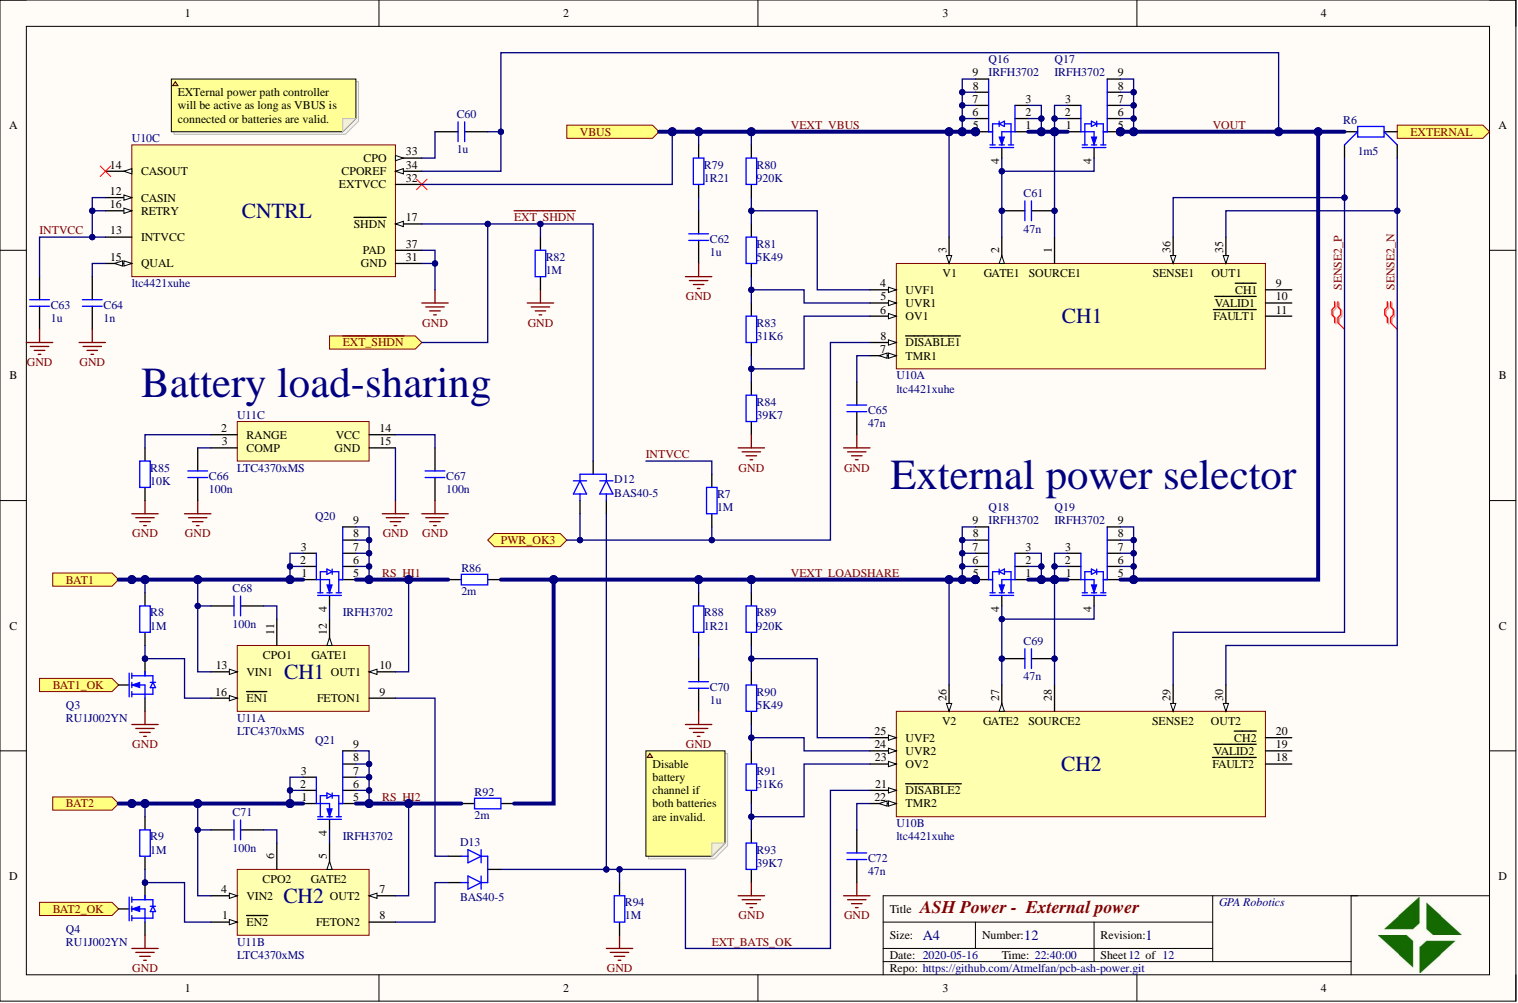
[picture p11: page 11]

EXTernal power path controller
will be active as long as VBUS is
connected or batteries are valid.

OUT1 35

TMR2 22

ASH Power - External power

2020-05-16 Time: 22:40:00 | Sheet of

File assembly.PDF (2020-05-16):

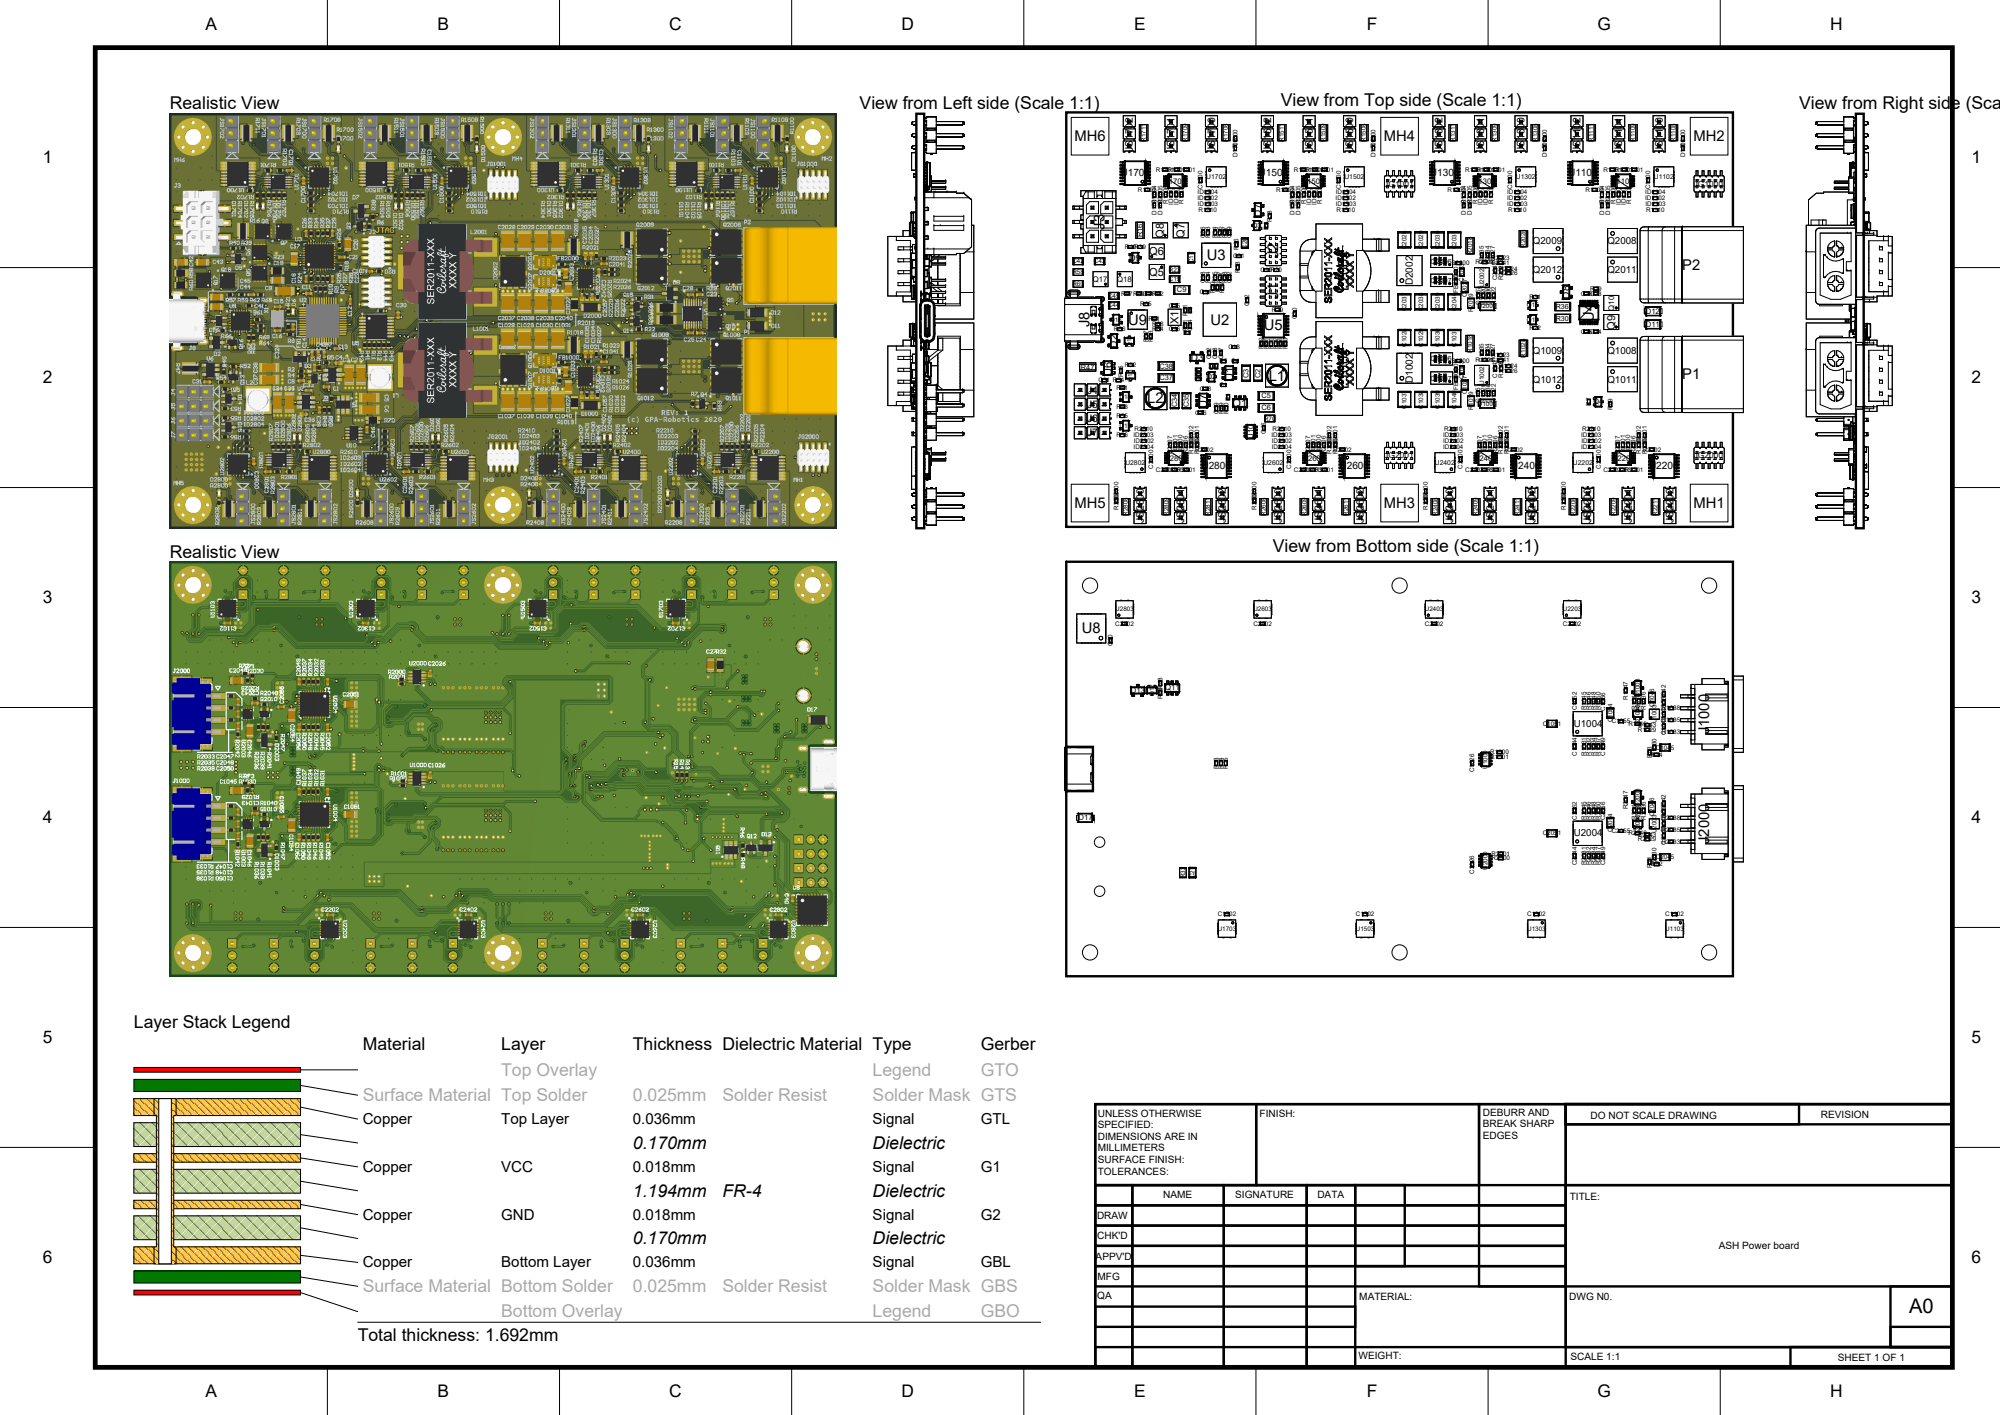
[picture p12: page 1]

View from Top side (Scale 1:1)

View from Bottom side (Scale 1:1)

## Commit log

2019-11-12 Started schematic
    [ash-power.PrjPCB, charger.SchDoc, control.SchDoc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]
2019-12-01 Added VAUX supply
    [ash-power.PrjPCB, aux_power.SchDoc, charger.SchDoc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]
2019-12-02 Started battery charging section
    [charger.SchDoc]
2019-12-02 Updated schematics
2020-01-14 Added MCU with supply and SWD
    [control.SchDoc]
2020-01-19 Almost done with main power distribution
    [ash-power.PrjPCB, aux_power.SchDoc, charger.SchDoc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]
2020-01-20 EXTernal supply finished
    [ext_power.SchDoc]
2020-01-22 Added USB-C circuit
    [ash-power.PrjPCB, power.SchDoc, usbpd_input.SchDoc]
2020-01-26 More work on power distribution
    [ash-power.PrjPCB, aux_power.SchDoc, charger.SchDoc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]
2020-01-26 Removed incorrect library link from projact and updated schematics
    [ash-power.PrjPCB]
2020-01-28 Almost finished schematic, started layout
    [ash-power.PrjPCB, aux_power.SchDoc, charger.SchDoc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]
2020-02-22 Layou 33% finished, schematic needs minor adjustments
    [ash-power.PrjPCB, aux_power.SchDoc, charger.SchDoc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]
2020-02-26 Added servo level converters and layout work
    [ash-power.PrjPCB, aux_power.SchDoc, control.SchDoc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]
2020-04-01 Initial charger layout
    [ash-power.PrjPCB, charger.SchDoc, control.SchDoc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]
2020-04-19 Removed charger circuitry
    [ash-power.PrjPCB, control.SchDoc, gan_buck.SchDoc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]
2020-05-03 Fixed VEXT power share control being inverted
    [ash-power.PrjPCB, control.SchDoc, ext_power.SchDoc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]
2020-05-06 Layout work
    [ash-power.PrjPCB, bom.csv]
2020-05-06 Minor layout changes
    [ash-power.PrjPCB]
2020-05-10 Layout: First draft complete
    [ash-power.PrjPCB, aux_power.SchDoc, gan_buck.SchDoc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]
2020-05-12 Added supplier links
    [ash-power.PrjPCB, bom.csv, gan_buck.SchDoc]
2020-05-16 Revision 1
    [ash-power.PrjPCB, aux_power.SchDoc, bom.csv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]
2020-05-16 Re-numbered schematic sheets
    [aux_power.SchDoc, control.SchDoc, cover.SchDoc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]
